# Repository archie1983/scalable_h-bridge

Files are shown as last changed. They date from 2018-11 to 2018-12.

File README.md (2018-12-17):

So this is a simple, scalable H-bridge, that I made on my own inspired by a design of an H-bridge in some chinese toy car.

Nothing special really- just a dual motor h-bridge. Circuits like this can be bought off the shelf on Ebay, Amazon and many other places, but mine can be customised. 
So for instance I needed 4.5A of current to drive my little DC130 motors at 7.5V, but I could only find 2A designs on Ebay for a reasonable price, so I made my own. And if I ever want 6A for instance, all I need to do, is add 8 more transistors to the output stage: 4x SS8050 and 4x SS8550.

Other design ideas for future include:
1) adding reverse diodes to the output transistors to be able to drive bigger motors.
2) Also it will be nice to incorporate a microcontroller on the same board at some point in the future.
3) Ballast resistors may need to be added to each of the output stage transistors to guarantee that they channel equal amounts of current.

The project was designed in KiCad 5.0.1.

Please feel free to use and improve it.

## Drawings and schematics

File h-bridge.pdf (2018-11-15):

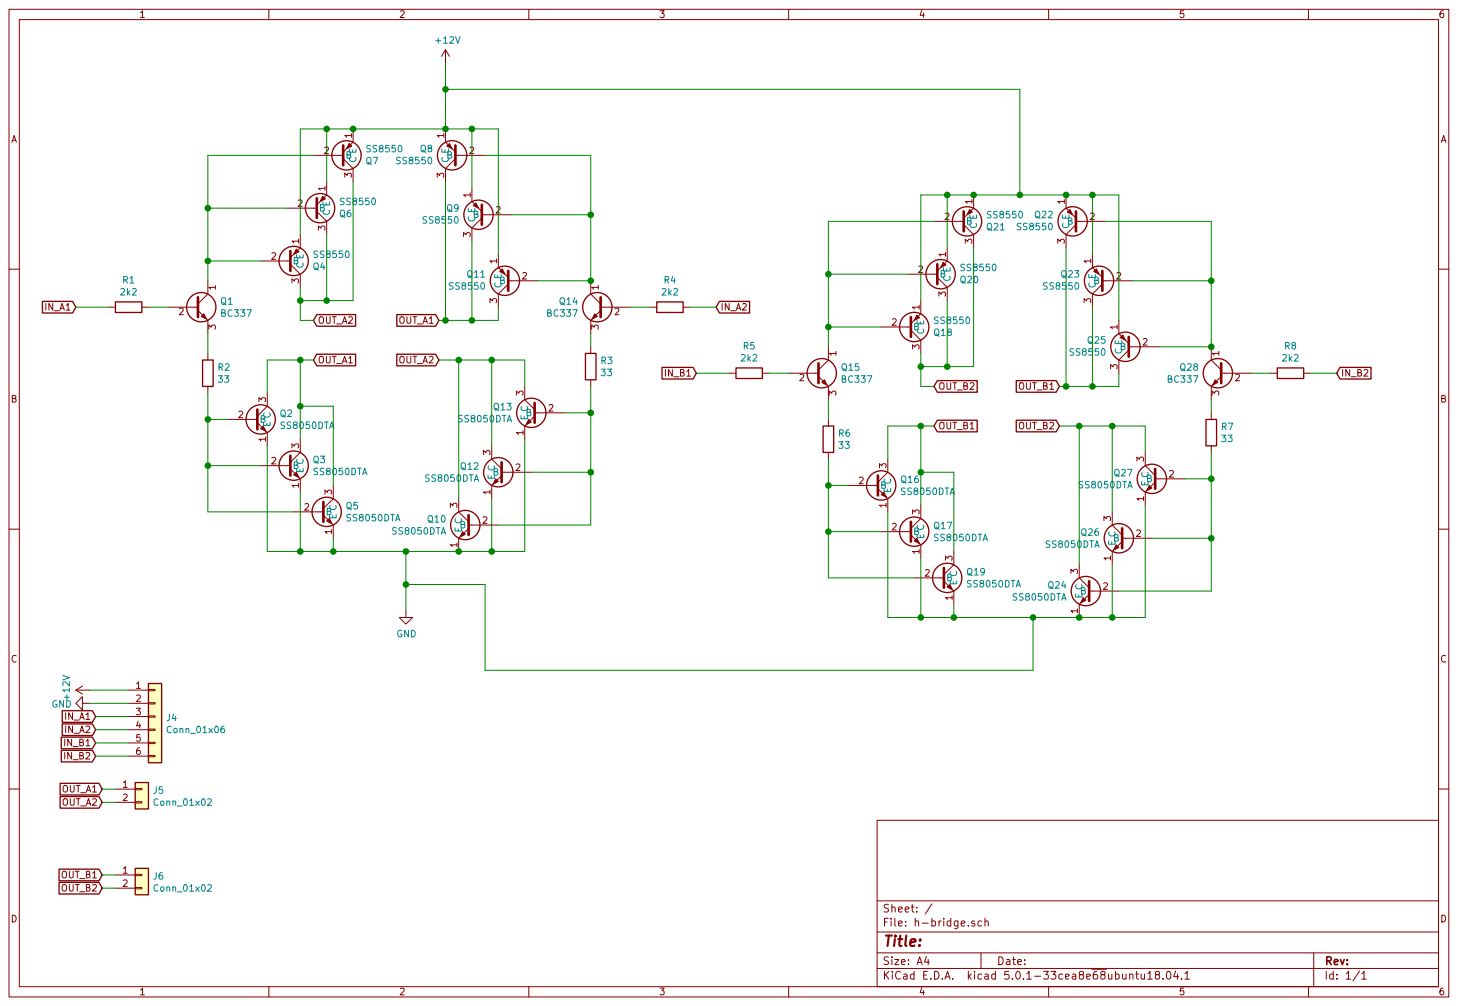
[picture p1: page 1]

File: h-bridge.sch Sheet: /
Id: 1/1 Title:

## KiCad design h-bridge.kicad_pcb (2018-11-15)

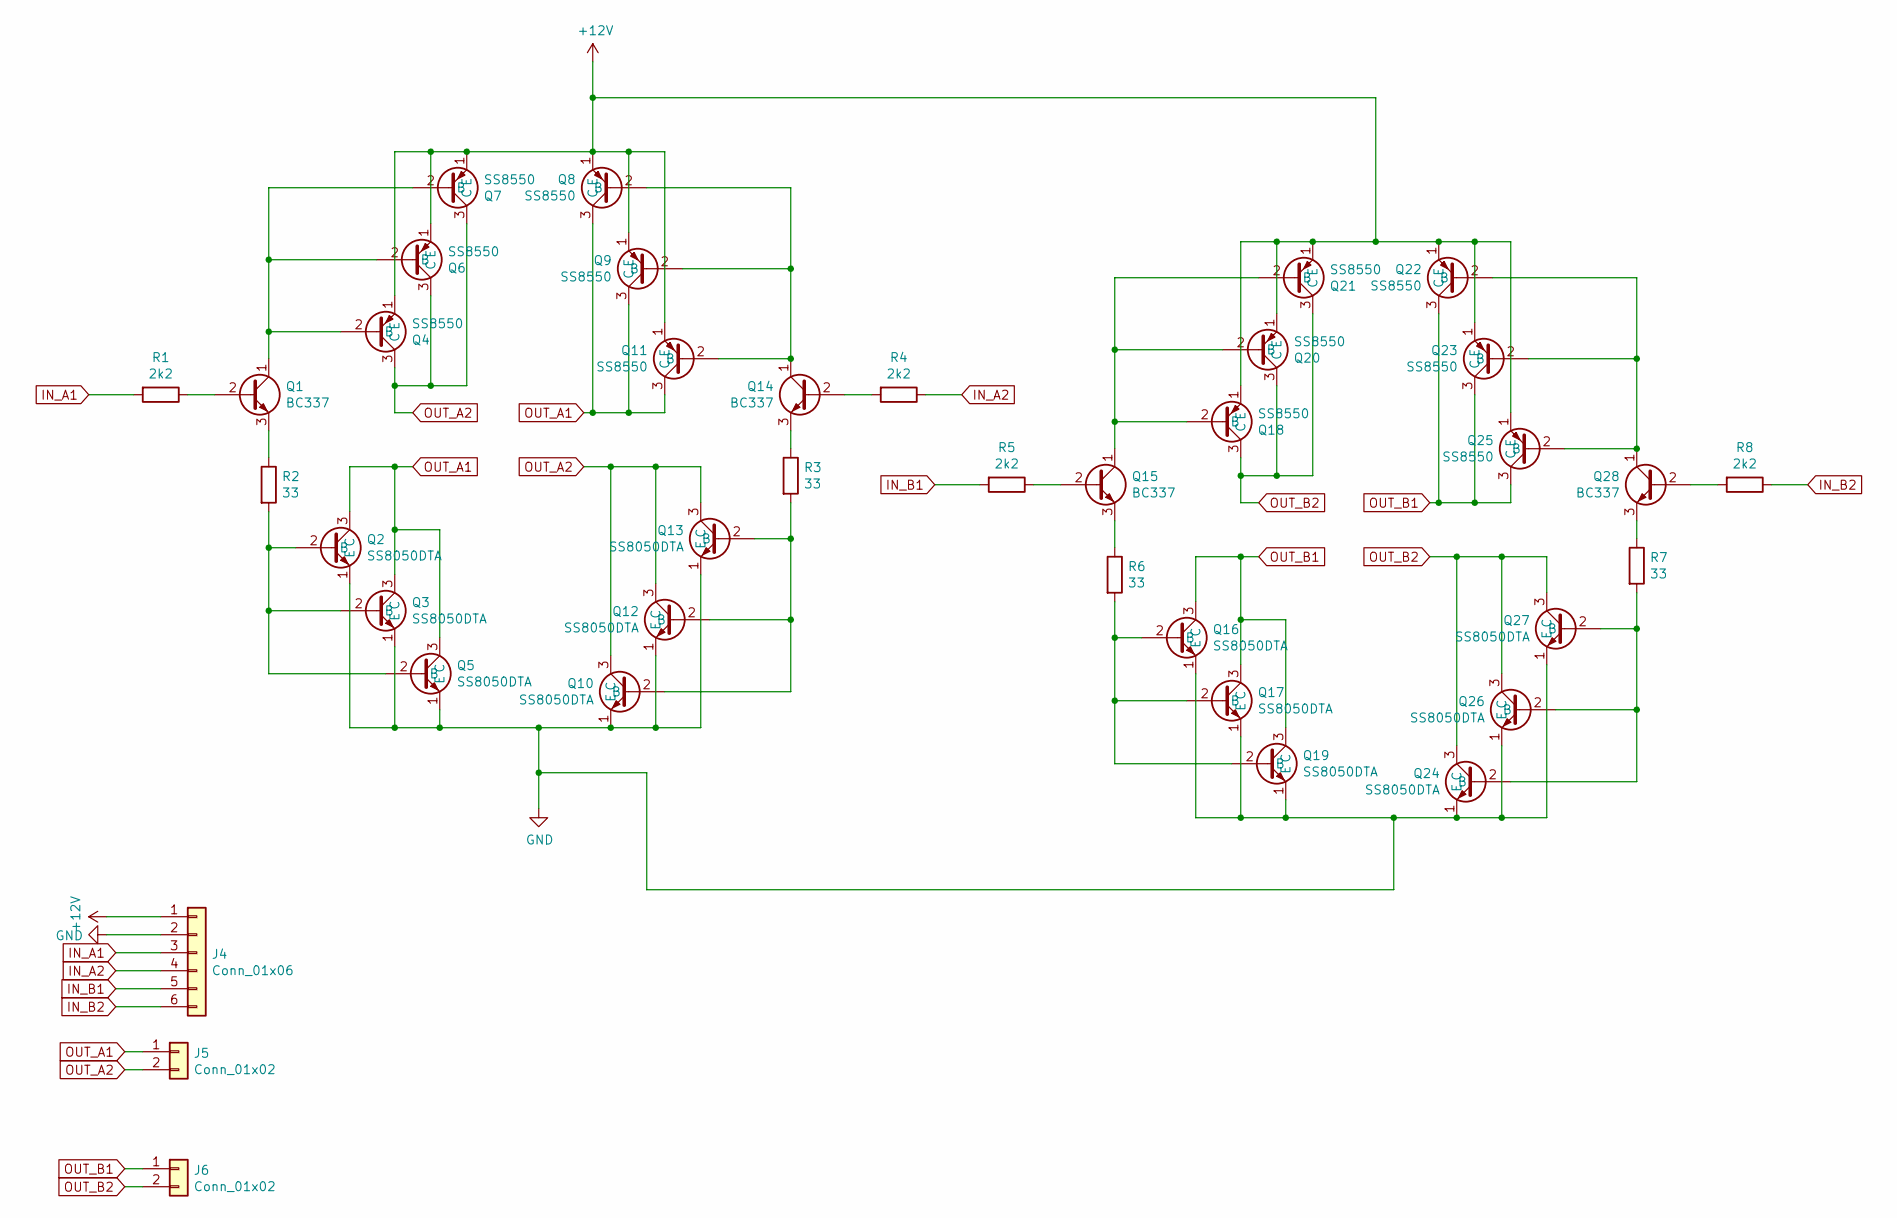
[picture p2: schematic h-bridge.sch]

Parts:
J4: Conn_01x06; PinHeader_1x06_P2.54mm_Vertical
J5, J6: Conn_01x02; PinHeader_1x02_P2.54mm_Vertical
Q1, Q14, Q15, Q28: BC337; TO-92_Inline_Wide
Q2, Q3, Q5, Q10, Q12, Q13, Q16, Q17, Q19, Q24, Q26, Q27: SS8050DTA; TO-92_Inline_Wide
Q4, Q6, Q7, Q8, Q9, Q11, Q18, Q20, Q21, Q22, Q23, Q25: SS8550; TO-92_Inline_Wide
R1, R4, R5, R8: 2k2; R_Axial_DIN0207_L6.3mm_D2.5mm_P5.08mm_Vertical
R2, R3, R6, R7: 33; R_Axial_DIN0414_L11.9mm_D4.5mm_P5.08mm_Vertical

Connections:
+12V: J4.1, Q4.1 (E), Q6.1 (E), Q7.1 (E), Q8.1 (E), Q9.1 (E), Q11.1 (E), Q18.1 (E), Q20.1 (E), Q21.1 (E), Q22.1 (E), Q23.1 (E), Q25.1 (E)
GND: J4.2, Q2.1 (E), Q3.1 (E), Q5.1 (E), Q10.1 (E), Q12.1 (E), Q13.1 (E), Q16.1 (E), Q17.1 (E), Q19.1 (E), Q24.1 (E), Q26.1 (E), Q27.1 (E)
IN_A1: J4.3, R1.2
IN_A2: J4.4, R4.1
IN_B1: J4.5, R5.2
IN_B2: J4.6, R8.1
unnamed: Q1.1 (C), Q4.2 (B), Q6.2 (B), Q7.2 (B)
unnamed: Q1.2 (B), R1.1
unnamed: Q1.3 (E), R2.1
unnamed: Q2.2 (B), Q3.2 (B), Q5.2 (B), R2.2
unnamed: Q10.2 (B), Q12.2 (B), Q13.2 (B), R3.2
unnamed: Q8.2 (B), Q9.2 (B), Q11.2 (B), Q14.1 (C)
unnamed: Q14.2 (B), R4.2
unnamed: Q14.3 (E), R3.1
unnamed: Q15.1 (C), Q18.2 (B), Q20.2 (B), Q21.2 (B)
unnamed: Q15.2 (B), R5.1
unnamed: Q15.3 (E), R6.1
unnamed: Q16.2 (B), Q17.2 (B), Q19.2 (B), R6.2
unnamed: Q22.2 (B), Q23.2 (B), Q25.2 (B), Q28.1 (C)
unnamed: Q24.2 (B), Q26.2 (B), Q27.2 (B), R7.2
unnamed: Q28.2 (B), R8.2
unnamed: Q28.3 (E), R7.1
OUT_A1: J5.1, Q2.3 (C), Q3.3 (C), Q5.3 (C), Q8.3 (C), Q9.3 (C), Q11.3 (C)
OUT_A2: J5.2, Q4.3 (C), Q6.3 (C), Q7.3 (C), Q10.3 (C), Q12.3 (C), Q13.3 (C)
OUT_B1: J6.1, Q16.3 (C), Q17.3 (C), Q19.3 (C), Q22.3 (C), Q23.3 (C), Q25.3 (C)
OUT_B2: J6.2, Q18.3 (C), Q20.3 (C), Q21.3 (C), Q24.3 (C), Q26.3 (C), Q27.3 (C)

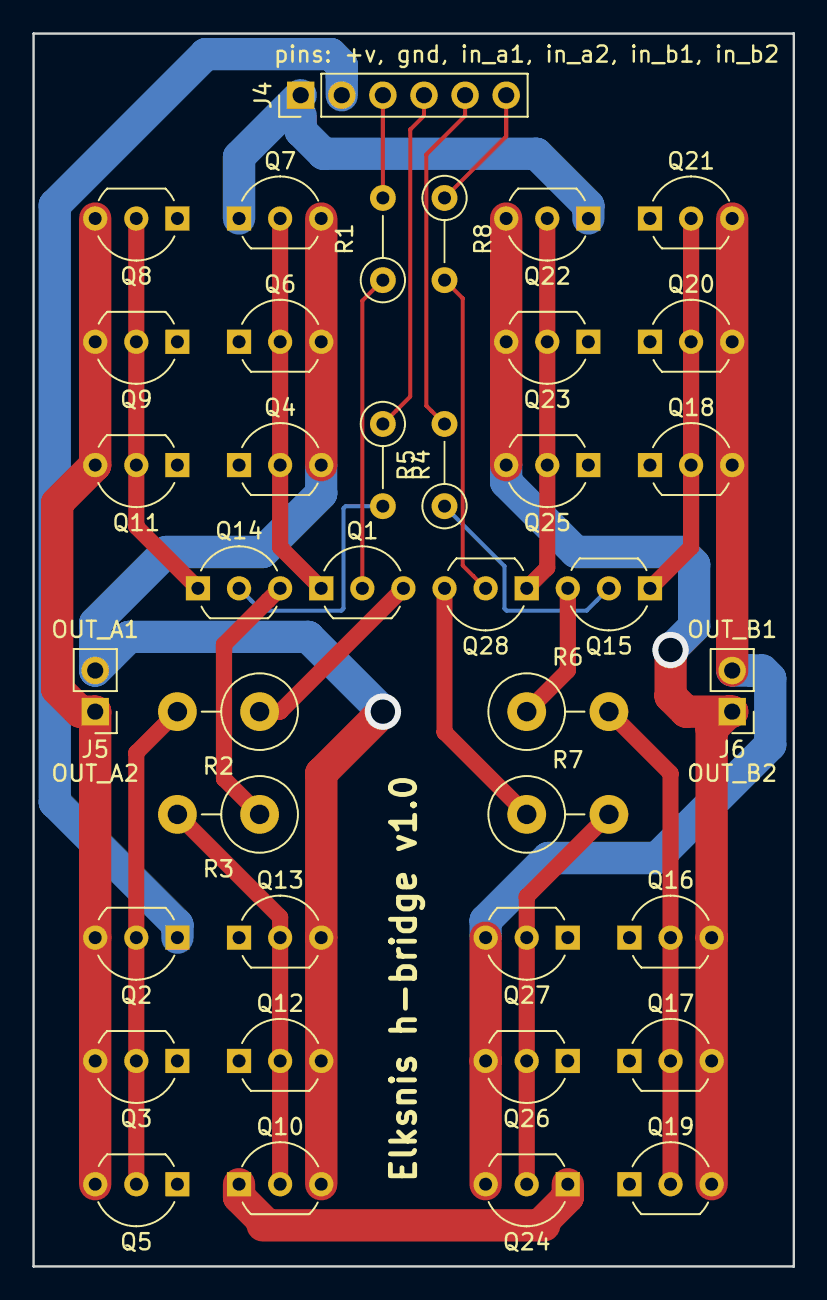
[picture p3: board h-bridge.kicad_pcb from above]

Board: 2 copper layers, 47.0 x 76.2 mm, 39 parts (0 on the bottom side), 26 nets.

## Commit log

2018-11-15 First commit of my h-bridge project. All ready for first prototype. Gerbers and drill files were sent to JLCPCB and boards manufactured.
    [h-bridge-B.CrtYd.gbr, h-bridge-B.Cu.gbr, h-bridge-B.Fab.gbr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]
2018-11-15 Added info about KiCad
